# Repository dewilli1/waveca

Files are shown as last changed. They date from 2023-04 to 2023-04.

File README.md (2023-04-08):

# WAter ValvE CAscade
A DIY box with a water in+out and 12V DC in+out, that can be cascaded. It shall be low-cost but provide basic l-safety. Hence, only one valve is used and water shall be connected in "parallel" while the cascading is referring to the current supply to reduce wiring (without dealing with wireless 
stuff). The box shall somehow be mounted on a bucket (plant pot without drain) to realize either an ebb and flow system (requiring a backflow) or simply allow refilling water to a certain level (with the minimum of the box's height). The function may double as a switch to controll a pump with a lower and an upper fluid level sensor.

It consists of
- housing (probably 3d-printed as I already fetched some cheap but oddly shaped components)
- pcb + some electronic parts
- floater, valve, maybe hose connector

## Requirements
### Housing
  - fluid resistant for pH-levels 3.0 to 8.5
  - keeps the pcb from overheating by direct sunlight
  - holds the pcb in a orientation no water drips on it
  
 ### Floater, valve, etc
  - cheap and 12V DC
  
 ### (main-)Board (referred to as pcb)
  - easy to solder
  - about half size of a credit card
  - "slides" into the housing
  - absorbs some mechanical force from the external sockets
  - manifests an electric circuit
  - temperature range is 270K to 320K ambient temperature
  
 ### electric circuit
  - shall never take more than 1.2 A
  - must not take more than 1W when incactive (forwarding current to the next box)
  - has 9-14 VDC supply voltage
  - a fluid level sensor is connected to a valve
  - the valve is open on the fluid side when a current flows through the coil
  - the fluid level sensor opens the electric connection when it's fluid level is exceeded
  - (optional:) a voltage of 5V to 16V resets the "state" which can be active or inactive
  
 #### description using a relay
  - the normally open (*NO*) port is used to pass current to the next cascade element
  - once the *NO* port is connected, it latches the present coil current
  - the normally connected (*NC*) port is used to power the valve (and the fluid level switch evaluation logic)
  - the coil current only needs to be "reset" when unpowering the entire cascade (if doubling as pump controller, it may still be required to reset it via 2nd fluid level switch)

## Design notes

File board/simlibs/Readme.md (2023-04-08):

# Libraries to run simulation

As Kicad has only very limited simulation support, we need some additional stuff for our some waveca components. As even the LT-Spice basics are missing, the schematics are created by LT spice, but they still require some changes. For some, a testbench may exists to directly verify it in kicad, including the transient simulation setup. The netlists for all asc's are modified to suit Kicad's LT-Spice compatibility requirements (figured out by trial and error) and collected in **subcircuits.lib**. It consists of the following models:

## G5V-1

The relay I bought actually to be connected directly to the switch. I picked some random coil wattage as trigger level and an arbitrary value for inductance as I haven't measured it yet.

## TBD
- The fluid level switch is not simulated yet, maybe a model triggers it after an imaginary capacitor is charged.
- The fluid valve is neither simulated yet, but a 24 ohms resistor may do.

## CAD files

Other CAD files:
case/body.blend
case/housings0.3.blend
case/pumphouse0.3.blend

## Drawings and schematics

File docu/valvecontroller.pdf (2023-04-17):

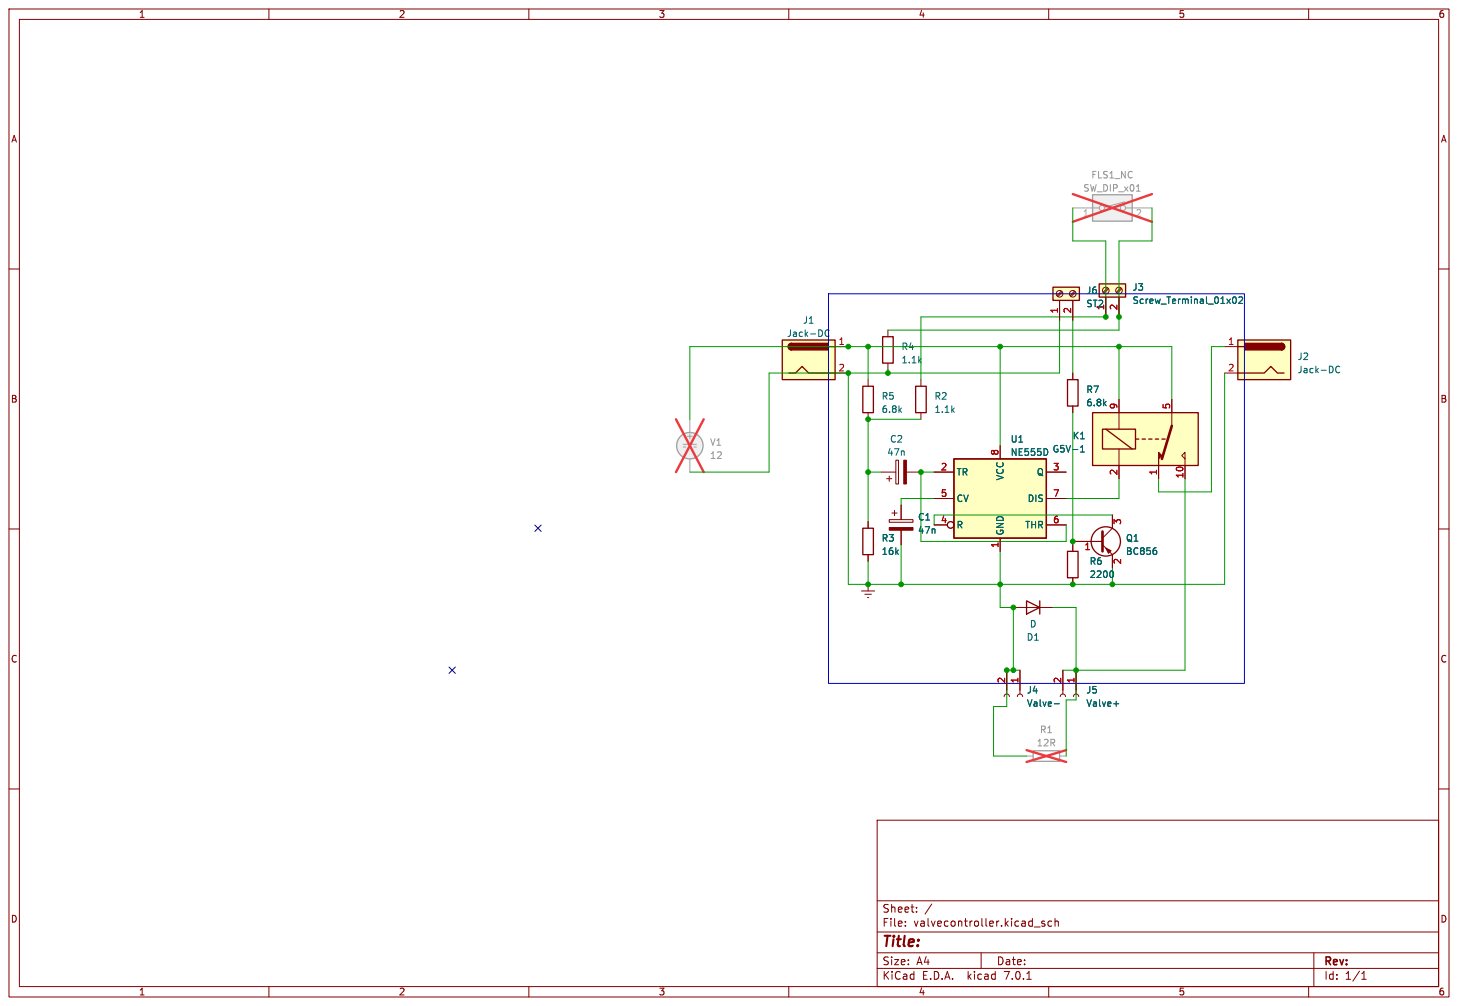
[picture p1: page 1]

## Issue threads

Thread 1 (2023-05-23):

findings after 1st printing

dewilli1, 2023-05-23:
- sinkhole for floater gasket 14mm x 1.9mm
- locknut for floater 13.3mm (2mm distance)
- wider hose clutch +3mm height, less sharp edges
- coupling for bottom parts: hook rather than notch
- narrower valve chamber; -9mm left, -2.5mm ríght
- larger screw holes
- second hole for counter screw bolt

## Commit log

2023-04-08 add layout with thyristor
    -may not be that failsafe
    -can't be simulated
    [thyristor.kicad_sch, valvecontroller.kicad_pcb, valvecontroller.kicad_sch]
2023-04-08 change to schmitt trigger
    this is (by mistake) for a closing fluid level switch
    [valvecontroller.kicad_sch]
2023-04-08 add simlib for relay
    not yet working, no pins
2023-04-08 fix relay model
    can now simulate a relay
    [valvecontroller.kicad_sch]
2023-04-08 adjust relay switch level by power
2023-04-08 add test bench for 1st lib model
    [g5vTestbench.kicad_sch]
2023-04-13 change path to relative
    [valvecontroller.kicad_sch]
2023-04-13 add model for valve
2023-04-14 add model for fluid level switch
    only falling edge works by now
2023-04-14 add rising edge model
    this actually already simulates a switch but the rest is needed for the slightly different switching-off behavior
2023-04-15 use ne555d
    this will not be able to reset. We need actually an opposite device or invert nearly every input
    [valvecontroller.kicad_sch]
2023-04-17 proposal1 for ne555 version
    the valve is no more switched directly, but while the relay is on
    [valvecontroller.kicad_sch]
2023-05-20 inner part of housing
    not yet detachable
    [body.blend]
2023-05-20 add hole for valve
    [body.blend]
2023-05-20 add retention screw hole
    [body.blend]
2023-05-21 add dc plug hole
    [body.blend]
2023-05-21 make body manifold
    [body.blend]
2023-05-21 cut off roof top
    [body.blend]
2023-05-21 add screw holes
    [body.blend]
2023-05-21 split housing in parts for printability
    [body.blend]
2023-05-21 enlarge bridge part
    [body.blend]
2023-05-31 increase bridge height by 12 mm
    (finding in issue #1)
    [body.blend]
2023-05-31 [WIP] ValveCase
    rework interconnection. Not yet done:
    - Interconnection on bridge
    - renew Screw hole
    [body.blend]
2023-07-05 add some working files for threefold housing
    [housings0.3.blend, pumphouse0.3.blend]
